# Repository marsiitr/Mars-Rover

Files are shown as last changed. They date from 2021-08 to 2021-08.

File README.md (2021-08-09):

# Mars-Rover

## Open Projects 2021   

## Abstract
<p align="justify">
 The <b>Mars Rover</b> is a small vehicle built to cover mars like uneven terrains. It is made to cover ueneven surfaces with ease and further to collect and analyze data. It has a robotic arm for data collection process and contains various sensors to recieve and record the data. It also has cameras, lidar and various other sensors for visual data interpretation and navigation.
</p>

<p align="center">
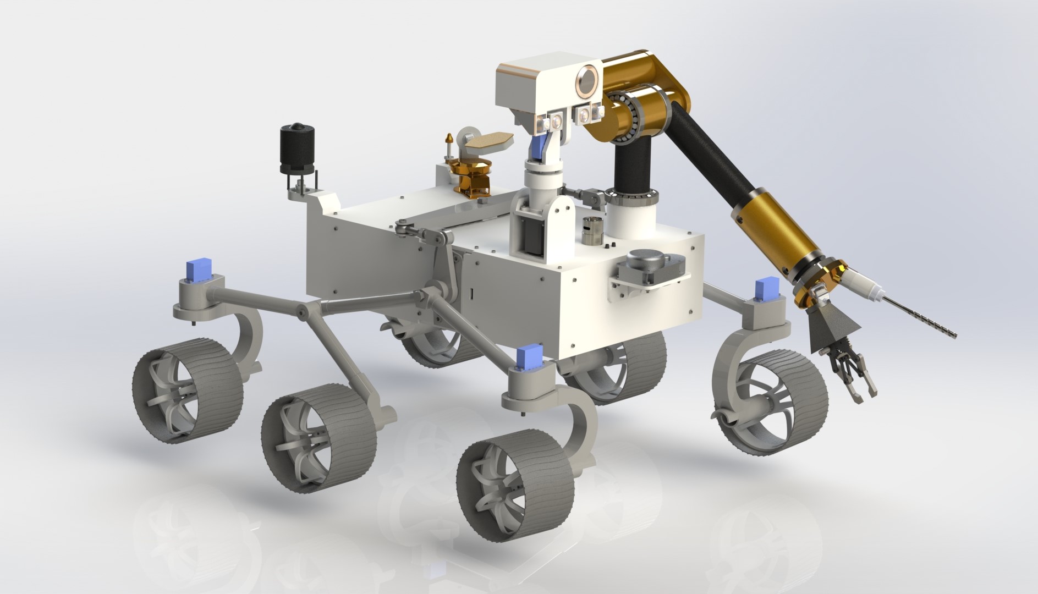
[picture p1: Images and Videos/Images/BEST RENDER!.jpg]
Mars Rover

 <i>Mars Rover</i>
</p>

## Motivation
The Mars rover project helps us to learn the mechanisms and functioning of an actual rover sent to Mars under various space programmes. 

<p align="justify">
 It gives us an insight on the <b>Rocker Bogie</b> suspension system which facilitates the best possible movement of the Rover on challenging terrains. It also compelled us to think about a mechainism for a compact and fully functioning robotic arm which would be used to collect sample data.
</p>

<p align="justify">
The project also sheds light on the various sensors used by the rover for data collection and analysis as well as for its navigation. <b>Lidar</b> and <b>PIXL</b> are the senosrs used by us in the rover. 
</p>

The project also helped us learn detailed CAD modelling using Solidworks.

## Mechanical aspects of design
 
### Chassis
<p align="justify">
The main body of the rover is built up using 20*20 sq.mm aluminium T slots as frames. It consists of a top and a bottom frame (each of 382 * 283 mm T slots) connected using a metal connector where the rocker bogie would be attached. Each rectangular frame is made up using 2 different pipes of length 382mm and 283 mm along with 2 extra 283mm pipes attached in between the frame to give it extra stability and support. It is then covered with ABS plastic covers which are attached to the frame using bolts and nuts.
</p>

<p align="center">  
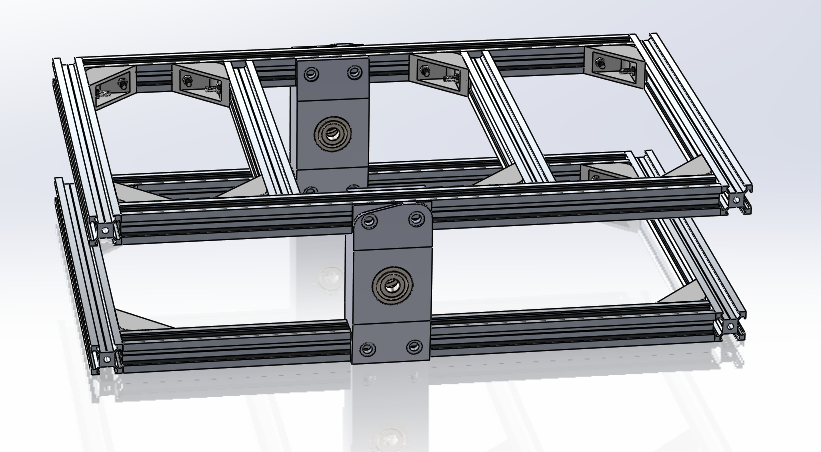
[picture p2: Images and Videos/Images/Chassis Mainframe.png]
Chassis
    
<i>Chassis</i>    
</p>  

### Rocker Bogie  
<p align="justify">
The Rocker Bogie is a six wheeled special suspension system used by the rover to ensure efficient motion on uneven terrains. It helps the mars rovers to overcome the rough terrains while maintaining stability by ensuring that all the wheel remain in contact with the ground. Each side of the suspension system is made up using 4 pipes of lengths 200, 170, 140 and 122mm(each of 314mm^2) which are connected using 3D printed connectors that facilitate the required motion of the suspension system. Both sides of the syspension are connected with the help of a differential bar placed on main frame of the rover. The middle of the bar is connected to the body with a pivot and the two ends are connected to the two rockers through some short links. If you hold the model rover body steady in midair and tilt one rocker up, one end of the bar will go back, the other end will go forward, and the other rocker will tilt down, thus maitaining the balance of the rover. 
</p>

<p align="center">
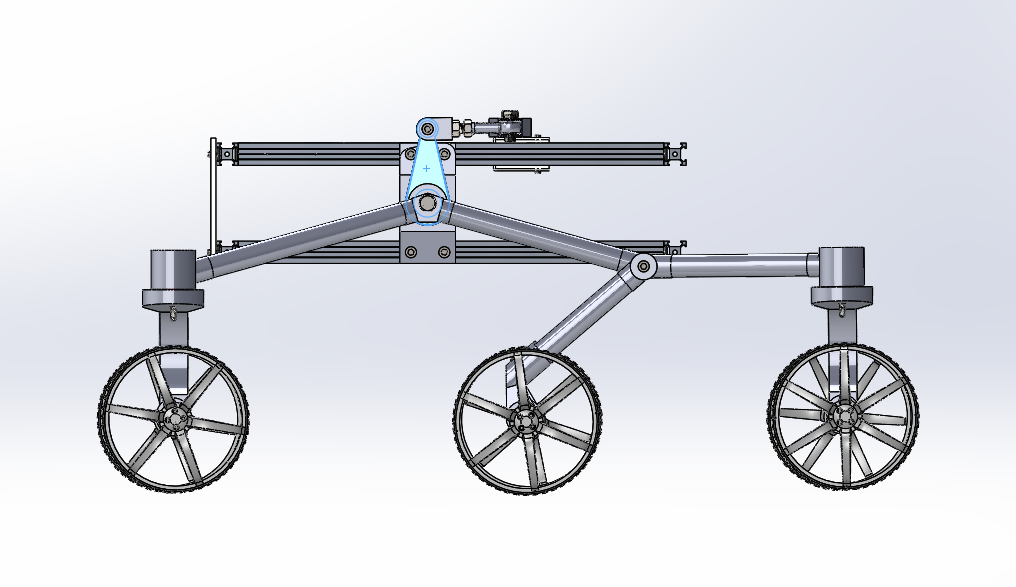
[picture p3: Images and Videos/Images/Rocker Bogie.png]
Rocker Bogie

 <i>Rocker Bogie</i>
</p>

### Robotic Arm
The robotic arm is equipped with three modules: a drill, a camera and a sample collector, installed on a rotating disc.

It has 4 degrees of freedom(DOFs) as follows:  
1.The base can be rotated 360 degrees.  
2.The rotational joint can be rotated 180 degrees (range is limited by the counterweight)  
3.The main link contains a hydraulic/pneumatic cylinder which is used to extend/shorten the length of the link. The length of the link has a range of 33-43 cm.   
4.The rotating disc is used to engage either the drill or the sample collector with the Martian surface at a time.  

Thus, in a way, we have a handle on the three polar coordinates:
1. The base varies the planar angle 'theta'
2. The rotational joint varies the vertical angle 'phi'
3. Hydraulic/pneumatic cylinder varies radial distance 'r'
This makes inverse kinematics relatively simpler.
 
<p align="justify">
The camera is used all the time for navigation of the arm as well as scanning of the martian surface
Servo motors are used for precise actuation.
An air compressor/pump embedded in the rover body is used to create the necessary pressure differential to operate the pneumatic/hydraulic cylinder.
</p>

<p align="center">
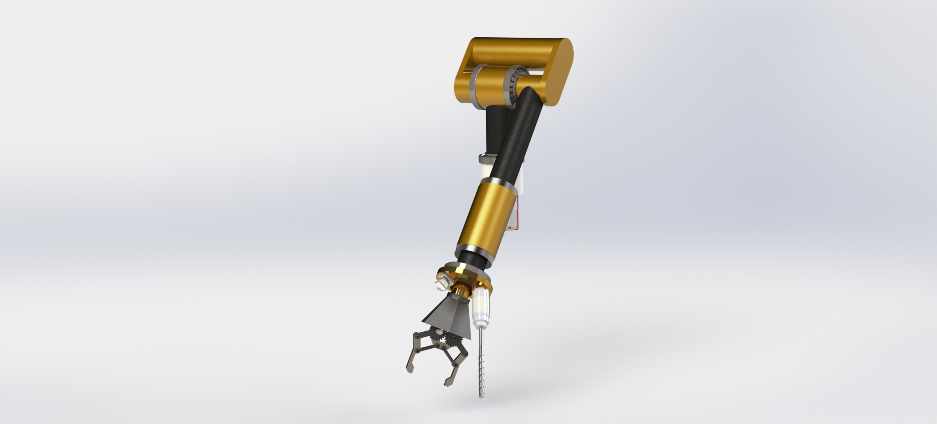
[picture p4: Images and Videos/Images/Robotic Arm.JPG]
Robotic Arm
  
<i>Robotic Arm</i>
</p>
                                                                                                                                                 
### Wheels
The wheel can be 3D by more flexible materials like thermoplastic elastomers which has high impact strength and

### Mast Cam
<p align="justify">
The bottom part of the mast contains the stepper motor which is fixed to the body. A shaft extends to the upper part of the mast which can rotate horizontally and lies on a cylindrical thrust bearing. The camera is attached to the mast with the servo motor for vertical rotation.
</p>

<p align="center">
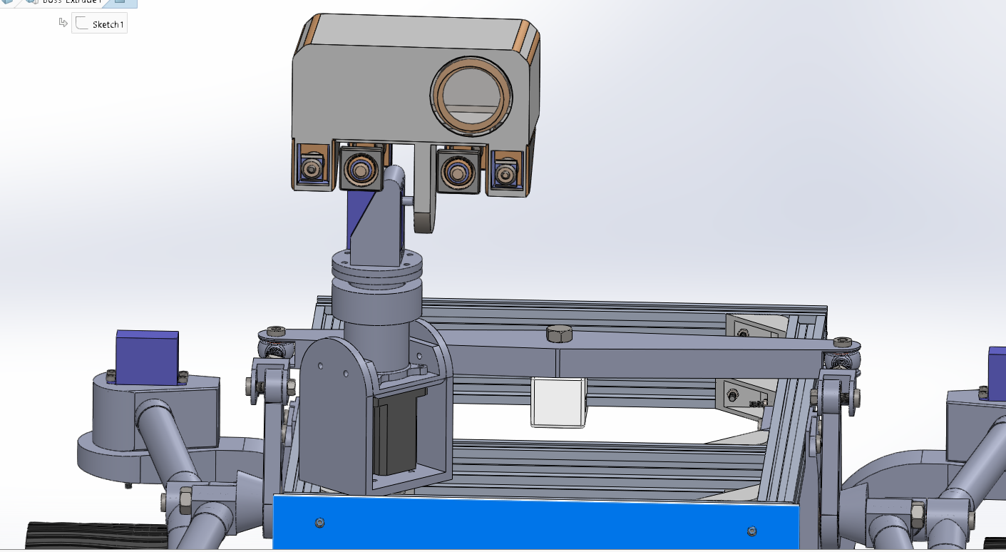
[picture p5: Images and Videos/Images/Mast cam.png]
Mast Cam
Mast Cam</i>
</p>

## CAD PARTS:
**IN CASE OF DISCREPANCY IN DOWNLOADING THE PARTS, KINDLY CHECK THE GIVEN DRIVE LINK:** https://drive.google.com/drive/folders/1dSjtfLlo9qPeHwJP8TGqEmEa5Fyg8wRc?usp=sharing

## Electronics aspects of design

### Sensors
1. **LIDAR sensor:**
<p align="justify">
Lidar is an acronym for “light detection and ranging.” It is sometimes called “laser scanning” or “3D scanning.” The technology uses eye-safe laser beams to create a 3D representation of the surveyed environment. This helps in navigation as well as analyzing the surrounding terrains and thus aids in the research part of the rover mission.
</p>

<p align="center">
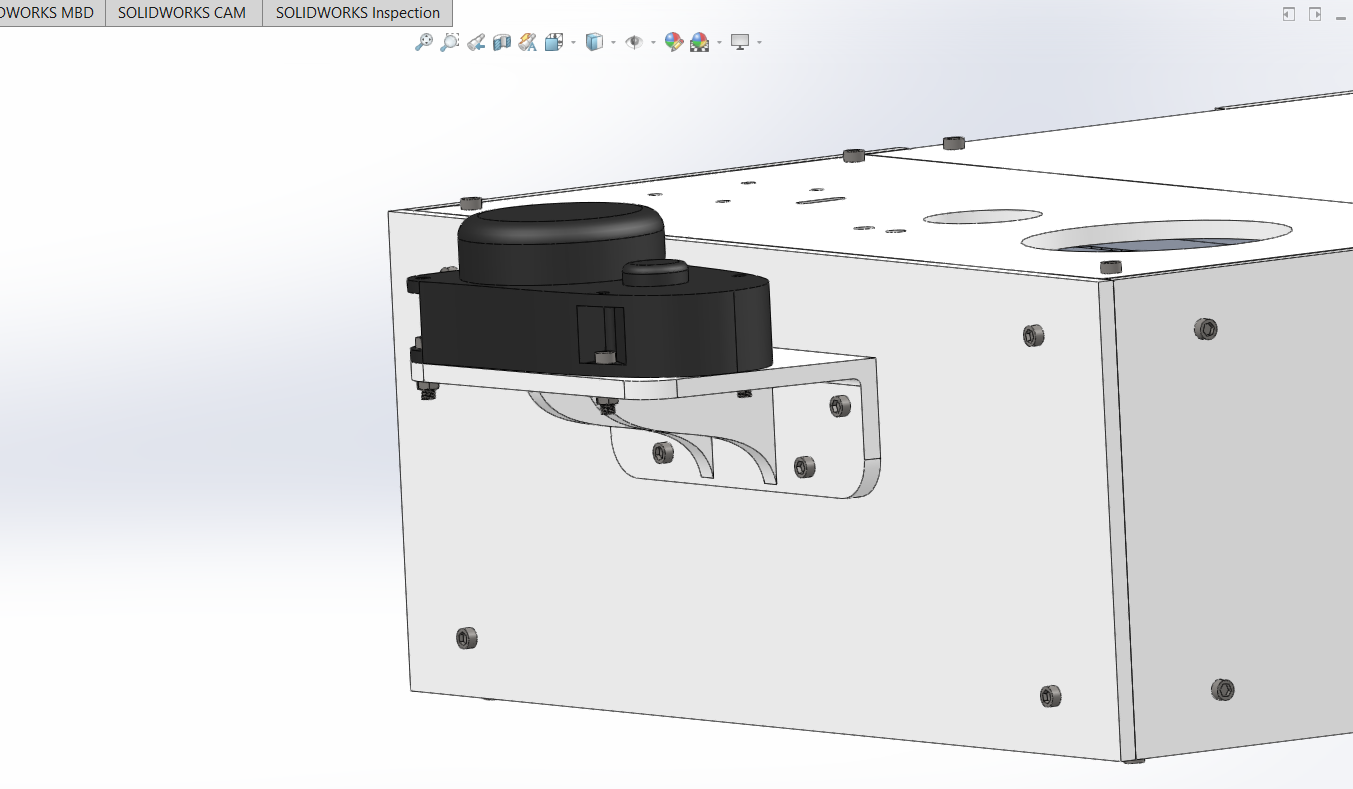
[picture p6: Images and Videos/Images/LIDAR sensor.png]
LIDAR Sensor

 <i> LIDAR Sensor</i>
</p>

2. **Mast Cam:**
<p align="justify">
The Mast Cam mounted over the chassis is used to get high definition videos and 3D-images of the surroundings which can be used for research purposes. It also has high zoom focus which can help in detailed examination of distant objects.
 </p>

3. **Robotic arm camera:**
<p align="justify">
A small camera is mounted on of the three modules of the robotic arm to assist in its motion and guide the drill to the required position. This makes teh collection of data sample more precise and accurate.
</p>

### Actuators
1. **DC motors:**
<p align="justify">
Six 12V DC motors with 20 RPM output are to be attached to the wheels which causes the locomotion of the Rover. The are placed in a holder attached to the Rocker Bogie and transmit torque to the wheels with the help of a small 3D printed shaft joining both these parts.
</p>

2. **Servo Motor:**
<p align="justify">
Four digital servo motors with 25kg cm torque output and operating voltage of 4.8-6.8 volts are used for steering the rover. The are attached to the rocker bogie with the help of a 3D printed holder connected on top of the dc motor holder. It enables the turning of front and rear pair of wheels and thus helps in turning the rover.
</p>

3. **Stepper motor:**
<p align="justify">
A 45kg-cm torque stepper motor is used for the horizontal rotation of the mast cam. The shaft of the stepper motor is attached to a threaded rod with a shaft coupler which transfers the rotation to the top part of the mast.
</p>

## Research part
<p align="justify">
We did an extensive research on the previously sent Mars Rovers and extracted details about the different components of the rover. We looked upon the structure and functioning of the parts and decided accordingly what to put in our rover. Although it was not practical to use all senosors and parts used by high end mars missions, we added whatever was possible in our reach to aid the research work of the rover.  
</p>

**This is the link of our initial research doc:** https://docs.google.com/document/d/1-jrgd7fFMnukzN-lmV8PeAjKU0p7QLTJImEPwY9DrF8/edit

## Cost Structure

| Components | Cost (in INR) |
|:---:|:---:|
| ABS plastic for 3d printing  | 16000 |
| T-slot Aluminium Extrussion | 360 |
| Battery  | 4300|
| Camera| 1500 |
| Stepper motors  | 725 |
| DC motors  | 3800 |
| Servo motors| 11250 |
| Servo horns | 375 |
| End joints | 800 |
| Nut and Bolts | 700 |
| Bearings | 900 |
| Lidar | 4850  |
| 4 thrust roller bearings| 3800 |
| Double acting mini pneumatic cylinder | 1258 |
| Single piston air compressor | 1000|
| Pneumatic tubing| 950 |
| Drill | 850 |
| Dc motor for drill: 15volt 11 watt | 3900 |
| Base servo motor 12volt  | 4950  |
| Joint servo motor 12volt |4950|
| Disc servo motor 12volt 2.9 watt| 3950 |
| Camera | 1250 |
| Sampler mechanism 5volt servo motor | 250 |
| Miscellaneous | 1500 |
|Total Cost| 74168 |

## Applications
1. The rover can be used to research the areas with highly uneven terrains and surfaces with ease due to its Rocker bogie suspension system.
2. It is equipped with a robotic arm and drill which enables sample data collection and storage.
3. The rover consists of a camera to take 3D images and high definition videos for mapping the terrain as well as analyzing it scientifically.
4. It can also be used to analyze the collected samples using the various sensors present on the rover

## Limitations
1. Speed of the rover is very low even on the flat terrains.
2. Battery life of the rover is short due to less charging capacity.

## Future Improvement
1. Better materials could be used instead of 3D printed plastic.  
2. Simulating the model in Gazebo and ROS.  

## Team members (with GitHub IDs)
1. <a href="https://github.com/matbot1">Avinash Singh</a>
2. <a href="https://github.com/MurkeyCube">Harikrishnan PB</a>
3. <a href="https://github.com/Pratyush-932">Pratyush Ojha</a>
4. <a href="https://github.com/SambitPrabhu">Sambit Prabhu</a>

## Mentors:
1.<a href="https://github.com/vanshgoyal">Vansh Goyal</a>

## Reference links
**Youtube-**  
<a href="https://www.youtube.com/watch?v=NOZZMsMAGh0&t=142s"> How I build mars rover replica </a>   
<a href="https://www.youtube.com/watch?v=McydwwR8xu4">[Mars Rover 2020 Perseverance] Body Assembly</a>  
<a href="https://www.youtube.com/watch?v=007SnaUxi40">JPL Mars Science Laboratory The Curiosity Rover</a>   

**Research links-**  
<a href="https://www.hindawi.com/journals/ijae/2016/5181097/"> Rocker Bogie Research </a>   
<a href="https://mars.nasa.gov/mars2020/spacecraft/rover/"> NASA Mars Rover (Perseverance) </a>   
<a href="https://llis.nasa.gov/lesson/11501">Actuator Design process for curiosity</a>     
<a href="http://robotics.estec.esa.int/ASTRA/Astra2004/Papers/astra2004_D-05.pdf">Types of Rocker Bogies</a>  
<a href="https://teamares.sserd.org/project_files/Ares_MCEV_Report.pdf"> Research paper for design of crew exploration vehicle on Mars</a>

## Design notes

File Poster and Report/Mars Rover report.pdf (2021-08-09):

# Mars Rover

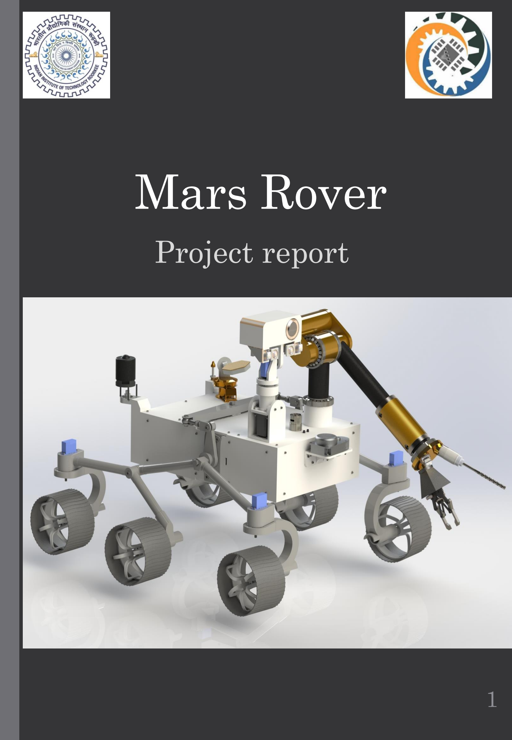
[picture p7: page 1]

## Project report

# INDEX

Team Members | -3
Abstract | -4
Motivation | -4
Research | -5
Mechanical Aspects | -6
Electronic Aspects | -13
Applications | -15
Limitations | -16

### Further Improvements -16

Reference Links | -17

# Mentor

### Avinash Singh

### Harikrishnan P B

### Pratyush Ojha

### Sambit Prabhu

# Team Members

### Vansh Goyal

# ABSTRACT

We have designed a mars rover capable of moving on rough terrains, with stable body frame and a fully functioning robotic arm, capable of drilling and collecting samples from the surface. The rover can move forward, backward and rotate. The navigation is done with the help of the mastcam which can orient itself in the desired direction.

# MOTIVATION

Having seen the successful landing of Mars missions, we were curious to find out how the rover is able to navigate in such harsh conditions and are able to carry out scientific missions on other planets.

# RESEARCH

1) In-depth study of NASA’s Perseverance and Curiosity Rover.
2) Components, instruments and features systematically documented.
3) Researched various types of suspension systems and we found the rocker bogie best as it requires less maintenance, and all the wheels stay in contact with the ground.
4) We chose the sensors required for the navigation of the rover.
5) The robotic arm was designed to be able to drill and collect the samples.
6) Most of the parts are designed to be 3D printed and can be assembled or disassemble easily.

# MECHANICAL ASPECTS

## 1) Chassis:

- The main frame of the rover is made by 20mm x 20mm T-slot Aluminium extrusion. The aluminium extrusions are connected with the help of 3D printed connectors.

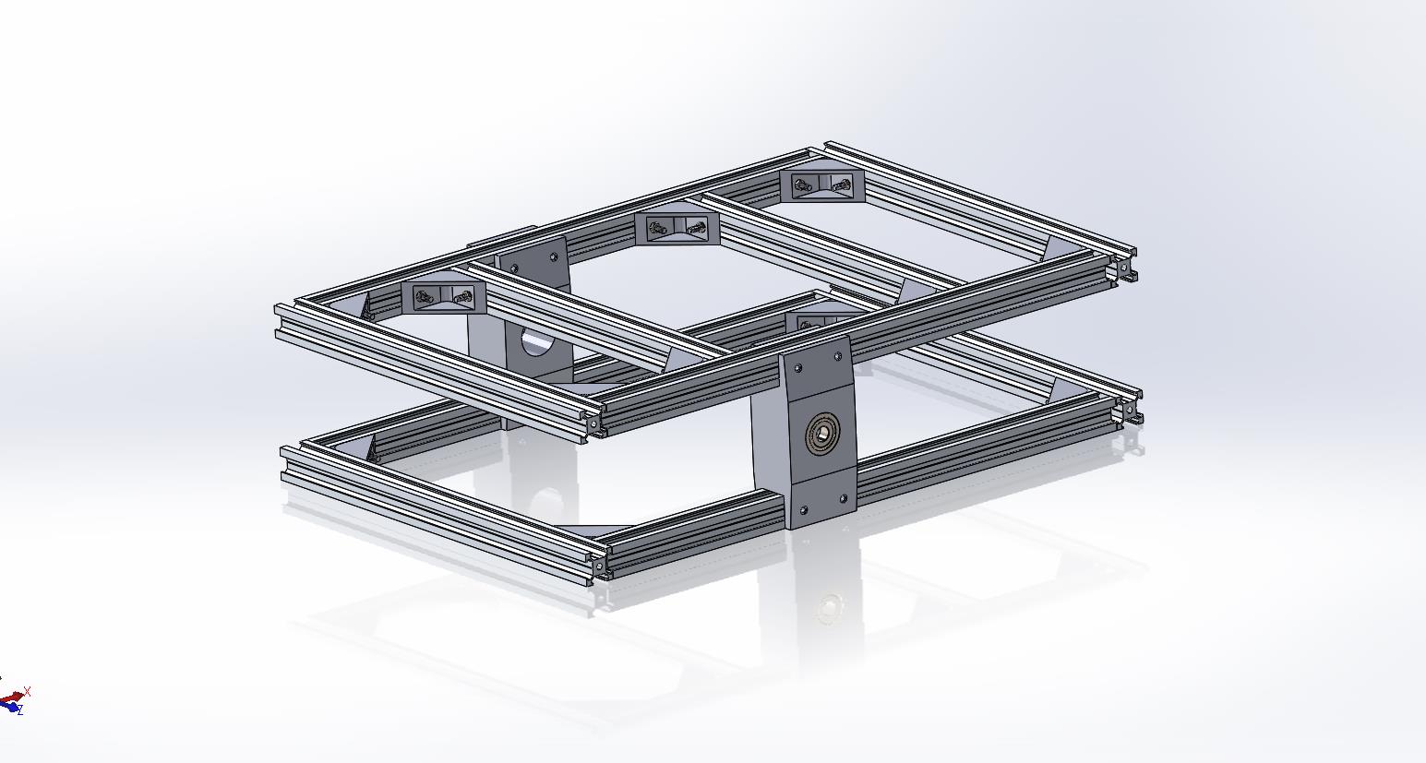
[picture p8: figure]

## 2) Rocker bogie:

- The rocker bogie
system maintains a
relatively constant
weight on each of
the rover's wheels.
The suspension also
minimizes rover tilt
as it drives, keeping
it more stable.

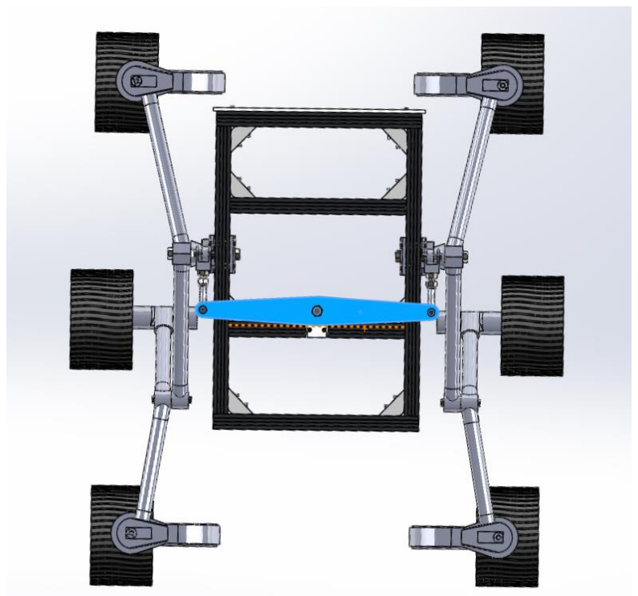
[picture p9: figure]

- The rocker bogie is made with a differential connected to the body of the rover for stability.
- The differential connects the left and right rockers and connects to the body of the rover by a pivot point in the centre of the rover’s top deck.

- We decided on 6 wheeled rocker bogie, so we have three main parts for the rocker bogie-
- The first one is the rocker which connects the front wheel to the differential and bogie in the rear.
- The second one is the bogie which connects the middle and rear wheel to the rocker.
- The third one is the connector for the front and back wheel to the rocker bogie for steering and rotation.

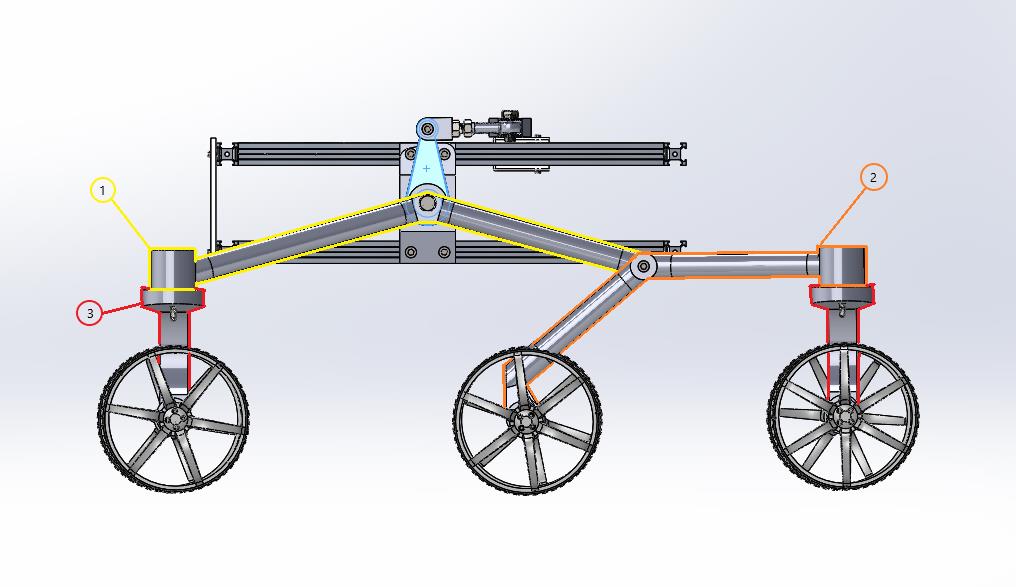
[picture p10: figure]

## 3) Wheel:

- The wheel can be 3D printed by more flexible materials like thermoplastic elastomers which has high impact strength and wear resistant.

## 4) Mastcam:

- the bottom part of the mast contains the stepper motor which is fixed to the body. A shaft extends to the upper part of the mast which can rotate horizontally and lies on a cylindrical thrust bearing. The camera is attached to the mast with the servo motor for vertical rotation.

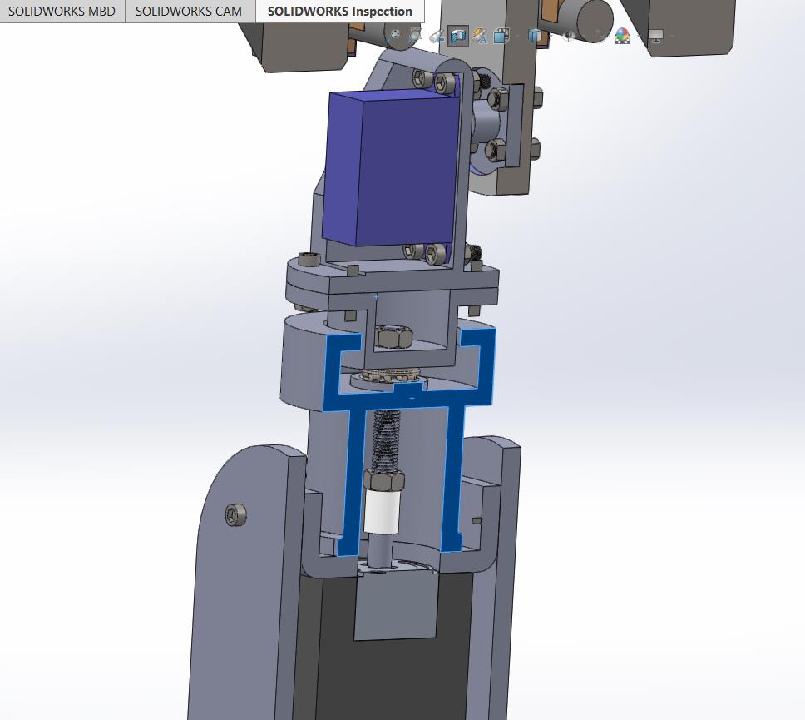
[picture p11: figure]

## 5) Robotic Arm:

- The robotic arm is
equipped with three
modules: a drill, a
camera and a
sample collector,
installed on a
rotating disc.

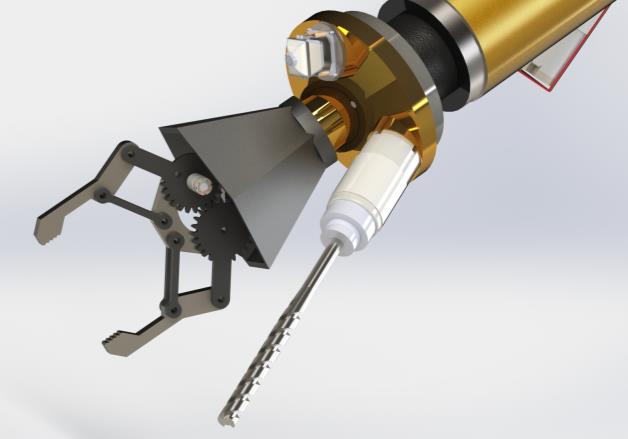
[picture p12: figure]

- It has 4 degrees of freedom(DOFs) as follows:
1) The base can be rotated 360 degrees.
2) The rotational joint can be rotated 180 degrees (range is limited by the counterweight)
3) The main link contains a hydraulic/pneumatic cylinder which is used to extend/shorten the length of the link. The length of the link has a range of 33-43 cm.

4)The rotating disc is used to engage either the drill or the sample collector with the Martian surface at a time.

Thus, in a way, we have a handle on the three polar coordinates:

1. The base varies the planar angle 'theta'
2. The rotational joint varies the vertical angle 'phi'
3. Hydraulic/pneumatic cylinder varies radial distance 'r'

This makes inverse kinematics relatively simpler.

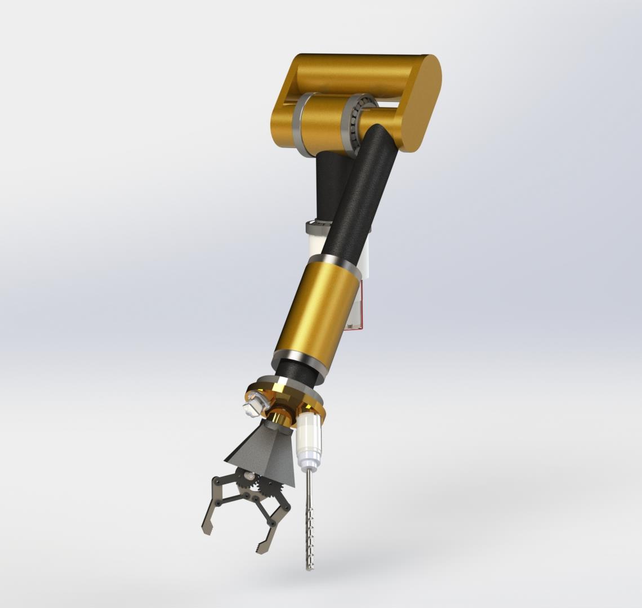
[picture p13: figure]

- The camera is used all the time for navigation of the arm as well as scanning of the Martian surface.
- Although the links of the robotic arm are light, the weights of the various motors and other
components in the end effector cause dynamic instability, which necessitates the usage of a counterweight.
- The counterweight provides frontback stability to the arm, as well as distributes the load between the two left-right bearings that are mounted on the base, so as to minimize the chances of
mechanical failure.
- Servo motors are used for precise actuation.
- An air compressor/pump embedded in the rover body is used to create the necessary pressure differential to operate the pneumatic/hydraulic cylinder.

# ELECTRONIC ASPECTS

## 1) Actuators:

a) 12V Brushless DC motors are attached to the wheels and used for the locomotion of the rover.
b) Servo motor is used for the movement of the corner four wheels, the head of the mastcam and in the robotic arm.
c) Stepper motor for the horizontal rotation of the camera. The shaft of the stepper motor is attached to a threaded rod with a shaft coupler which transfers the rotation to the top part of the mast.

## 2) SENSORS:

a) Mastcam:

It is used to take images and navigate the rover and can change its orientation to a desired location.

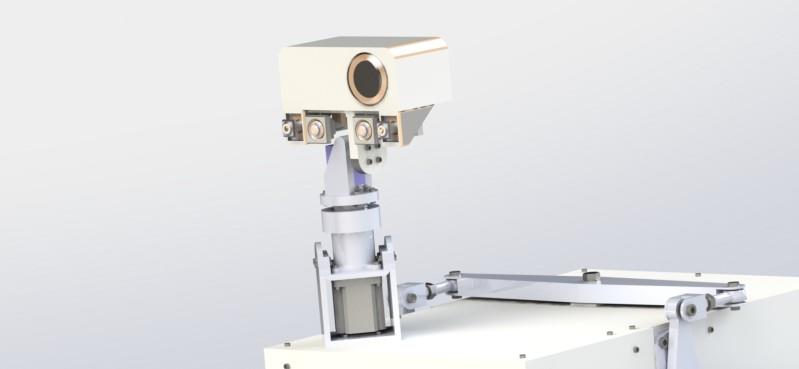
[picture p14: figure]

b) Lidar:

It is used for sensing the distance between the rover and its
surrounding and helps in
navigation.

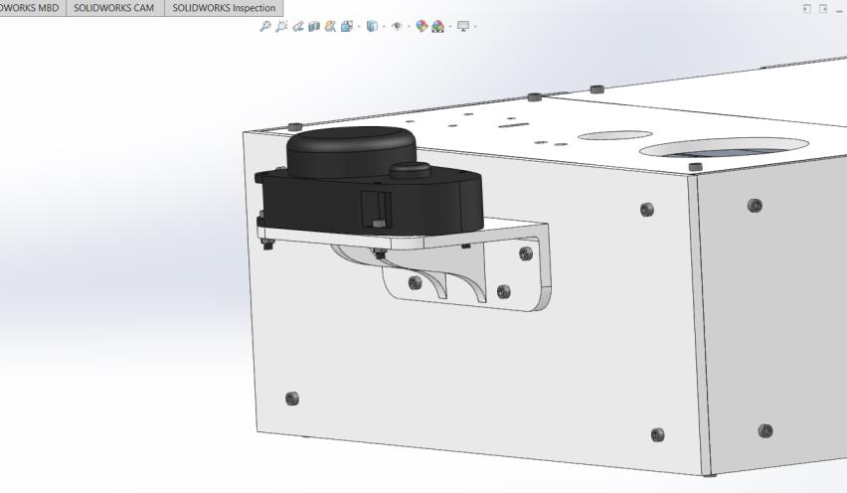
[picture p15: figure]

# APPLICATIONS

- The rover can be used to research the areas with highly uneven terrains and surfaces with ease due to its rocker bogie suspension system.
- It is equipped with a robotic arm and drill which enables sample data collection and storage. The rover consists of a camera to take 3D images and high-definition videos for mapping the terrain as well as analyzing it scientifically.
- It can also be used to analyze the collected samples using the various sensors present on the rover

# FUTURE IMPROVEMENTS

1) Better materials could be used instead of 3D printed plastic.
2) Simulating the model in Gazebo and ROS.

# LIMITATIONS

1) The speed of the rover is slow.
2) Life of the rover is short since the charging capacity is less.

# REFERENCE LINKS

Youtube-
- [Mars Rover 2020 Perseverance] Body Assemblyhttps://www.youtube.com/watch?v=McydwwR8xu4
- How I build mars rover replicahttps://www.youtube.com/watch?v=NOZZMsMAGh0&t=1 42s (https://www.youtube.com/watch?v=NOZZMsMAGh0&t=142s)
- JPL Mars Science Laboratory The Curiosity Roverhttps://www.youtube.com/watch?v=007SnaUxi40

Research links-
- https://www.hindawi.com/journals/ijae/2016/5181097/
- https://mars.nasa.gov/mars2020/spacecraft/rover/
- https://llis.nasa.gov/lesson/11501
- http://robotics.estec.esa.int/ASTRA/Astra2004/Papers/astra2004_D-05.pdf (http://robotics.estec.esa.int/ASTRA/Astra2004/Papers/astra2004_D-05.pdf)
- https://teamares.sserd.org/project_files/Ares_MCEV_Repo rt.pdf (https://teamares.sserd.org/project_files/Ares_MCEV_Report.pdf)

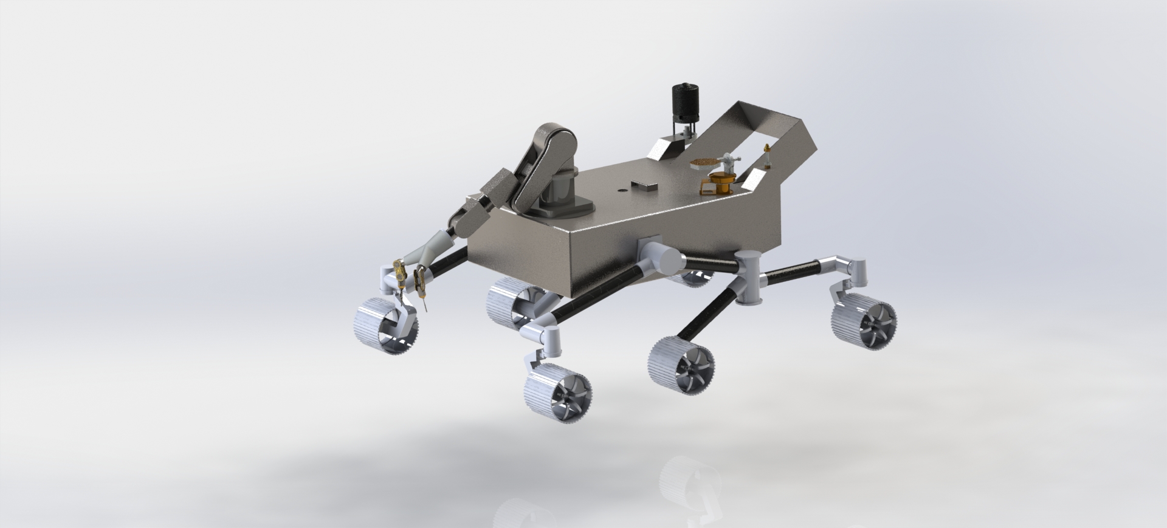
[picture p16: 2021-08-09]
Images and Videos/Images/Initial design (changed later).JPG

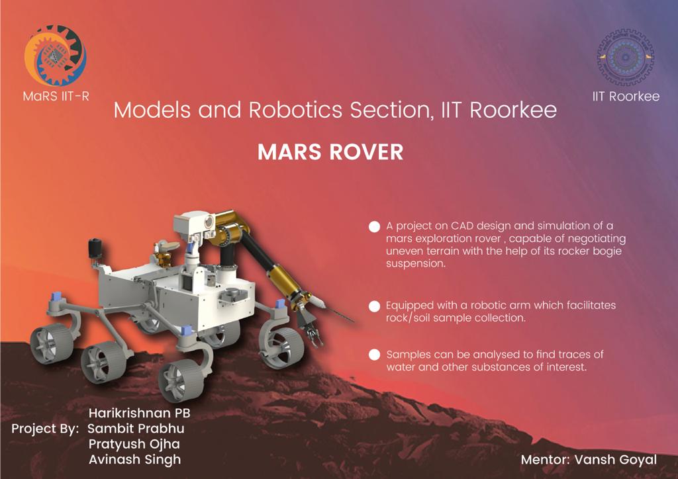
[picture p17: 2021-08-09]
Poster and Report/Poster.jpeg

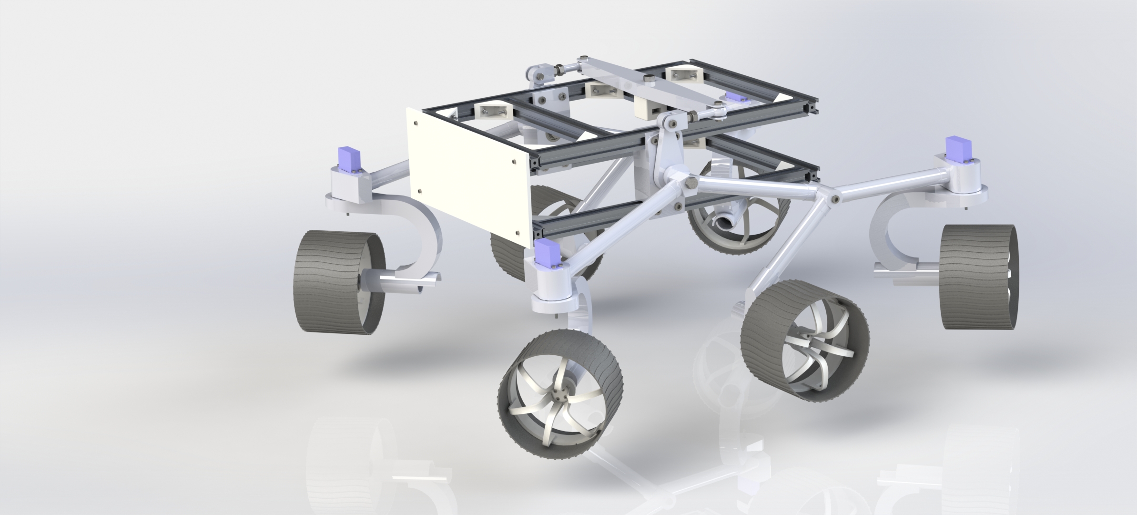
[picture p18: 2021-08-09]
Images and Videos/Images/Mars Rover 2.JPG

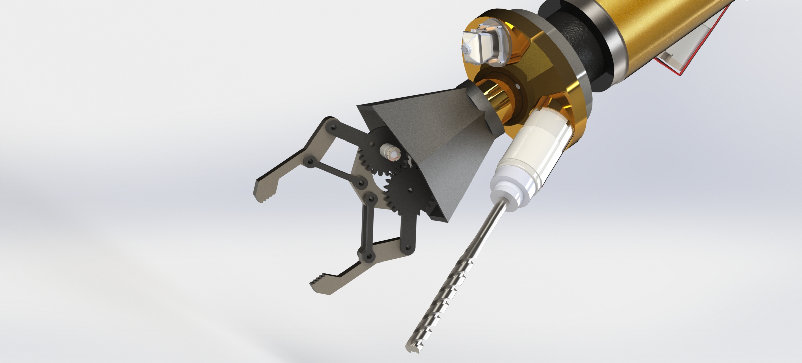
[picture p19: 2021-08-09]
Images and Videos/Images/Arm module.JPG

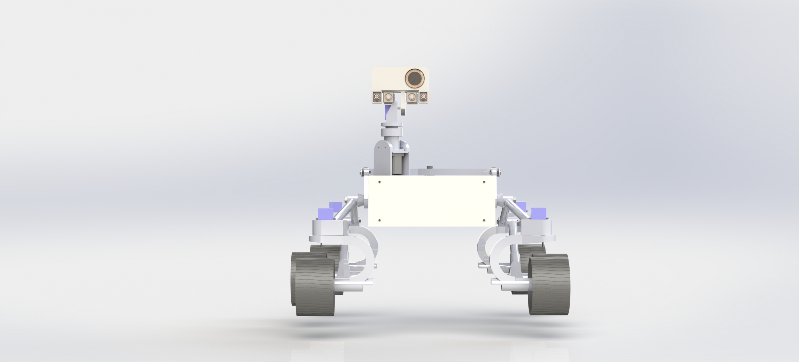
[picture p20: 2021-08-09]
Images and Videos/Images/camera 1.JPG

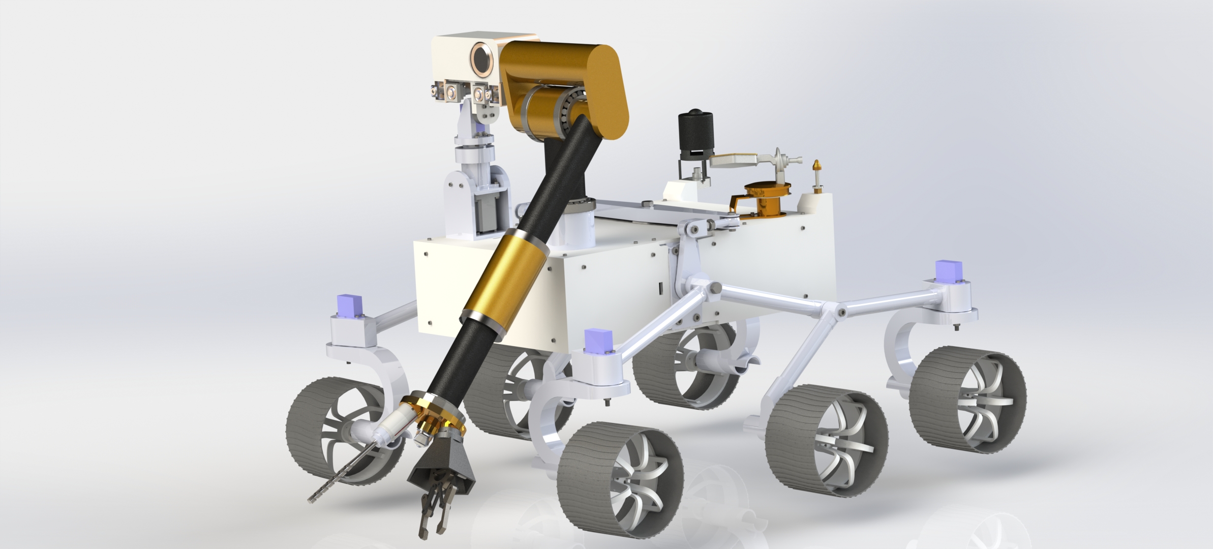
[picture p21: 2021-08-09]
Images and Videos/Images/rendered image 1.JPG

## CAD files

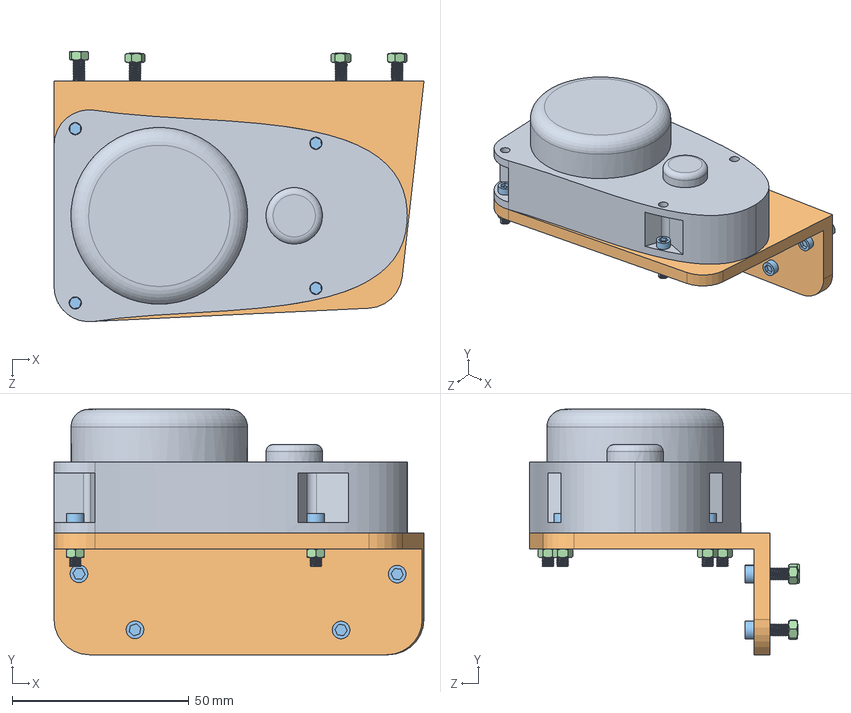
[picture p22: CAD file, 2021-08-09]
Mechanical design/Camera/Lidar/Lidar sensor.SLDASM
104.7 x 69.5 x 76.6 mm
Lidar
Stand for lidar
M3 bolt for camera-1 x 8
M3 nut x 8

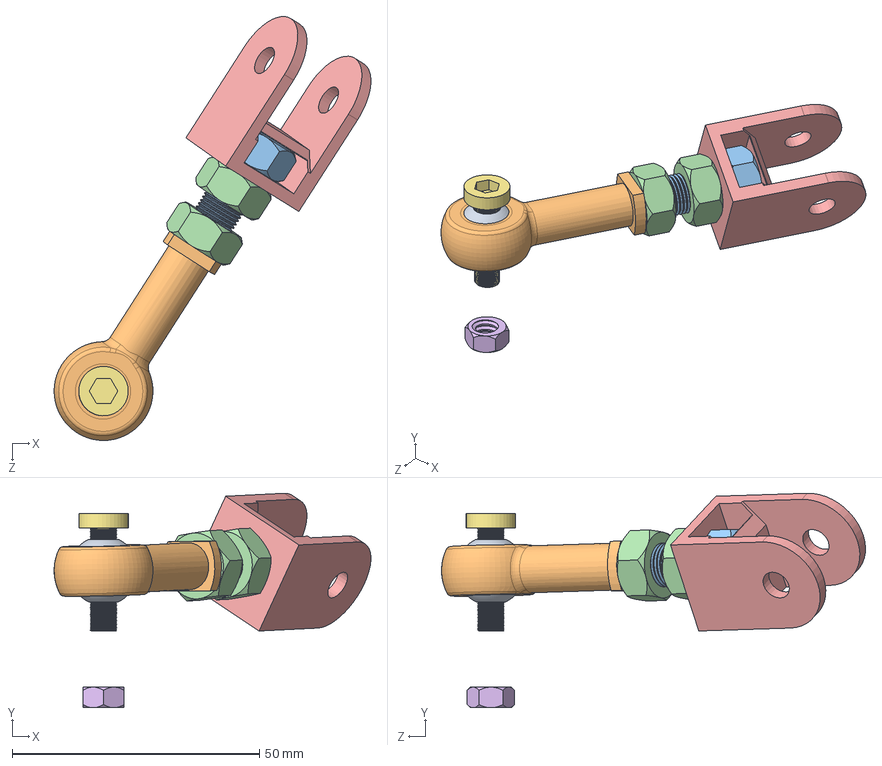
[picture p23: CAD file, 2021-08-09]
Mechanical design/Rocker Bogie/End joint bearing/End join bearing.SLDASM
64.1 x 43.3 x 85.7 mm
Ball
connector part
M8 Bolt for end joint
M8 Nut x 2
connector to rocker
M5 nut
M5 bolt for end joint

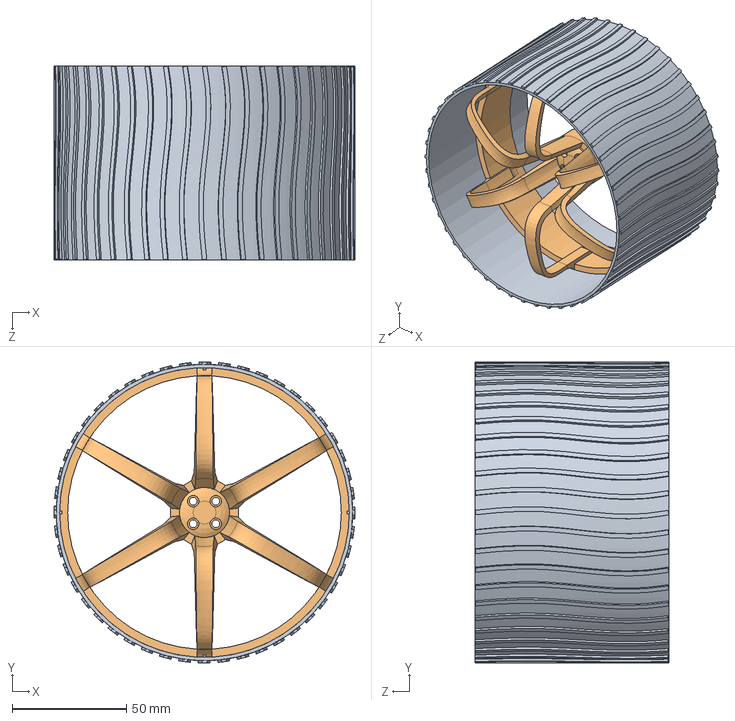
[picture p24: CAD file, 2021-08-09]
Mechanical design/Wheel.SLDASM
132.0 x 132.0 x 85.0 mm
Wheel Part-1
Wheel Part-2

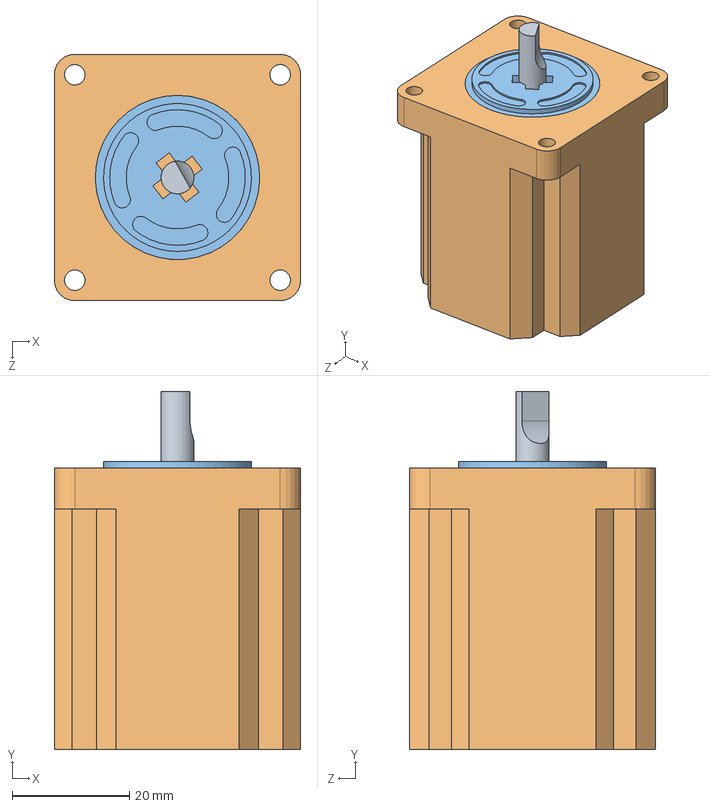
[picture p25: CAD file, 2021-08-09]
Mechanical design/Camera/Stepper motor/Stepper motor.SLDASM
42.0 x 61.0 x 42.0 mm
shaft for stpmotor
stepper motor-1
stepper motor-2

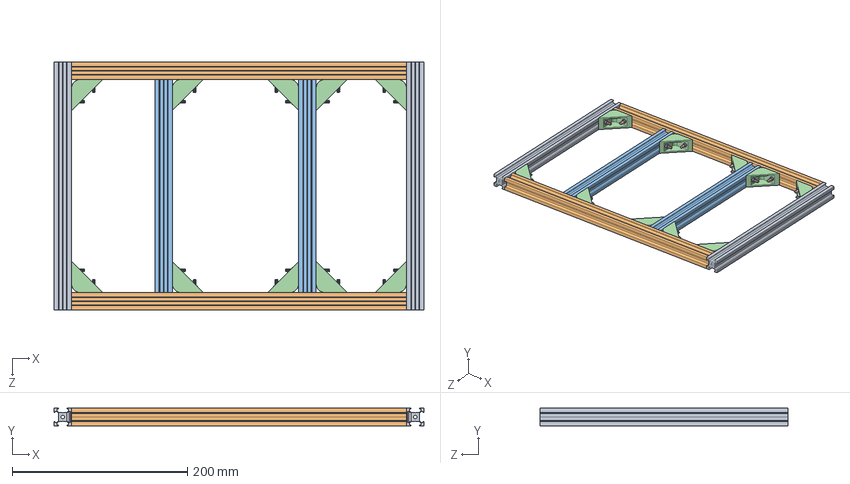
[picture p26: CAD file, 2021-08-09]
Mechanical design/Frame/Top Frame.SLDASM
422.0 x 20.0 x 283.0 mm
T-slot aluminium profiles(283) x 2
T-slot aluminium profiles(382) x 2
T-slot aluminium profiles(243) x 2
connector x 10
T-bolt x 20
hexagon nut style 1_is x 20

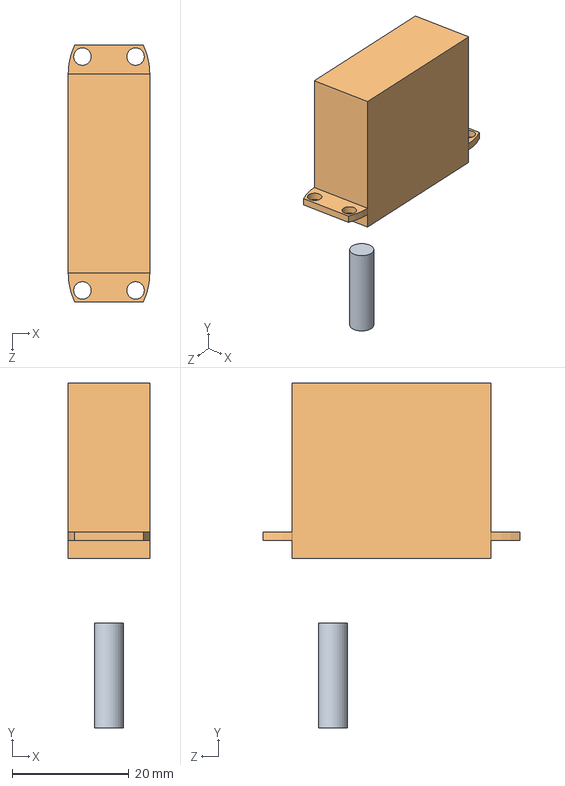
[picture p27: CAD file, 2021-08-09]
Mechanical design/Rocker Bogie/Motors/Servo Assembly.SLDASM
14.0 x 59.1 x 44.0 mm
servo shaft
Servo motor

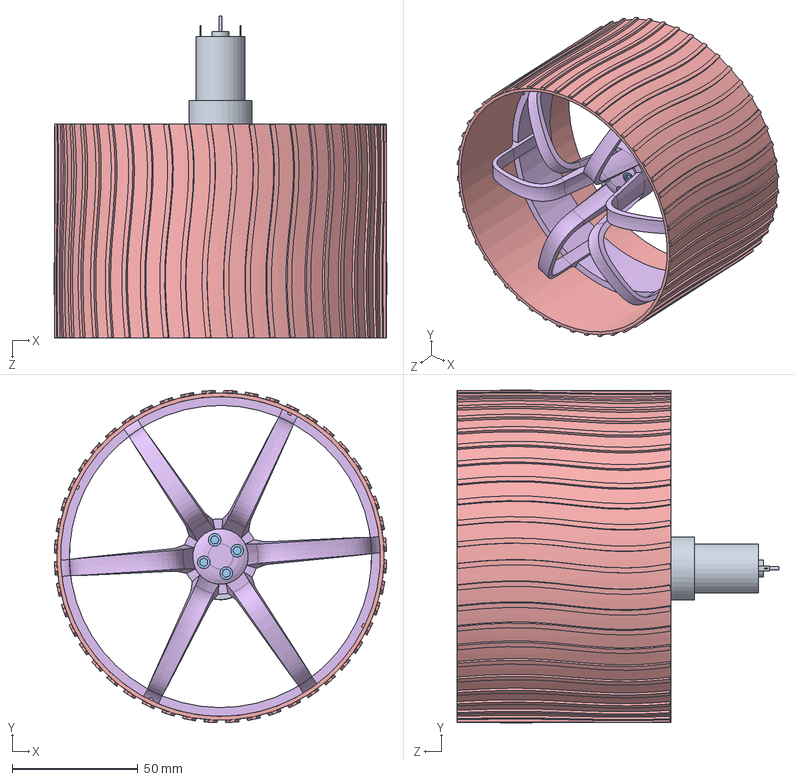
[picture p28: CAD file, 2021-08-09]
Mechanical design/Wheel + motor for centre.SLDASM
132.1 x 132.1 x 127.9 mm
Wheel motor(RH)
connector to wheel(RH)
M3 bolt for wheels(RH) x 4
M3 nut x 4
Wheel Part-1
Wheel Part-2

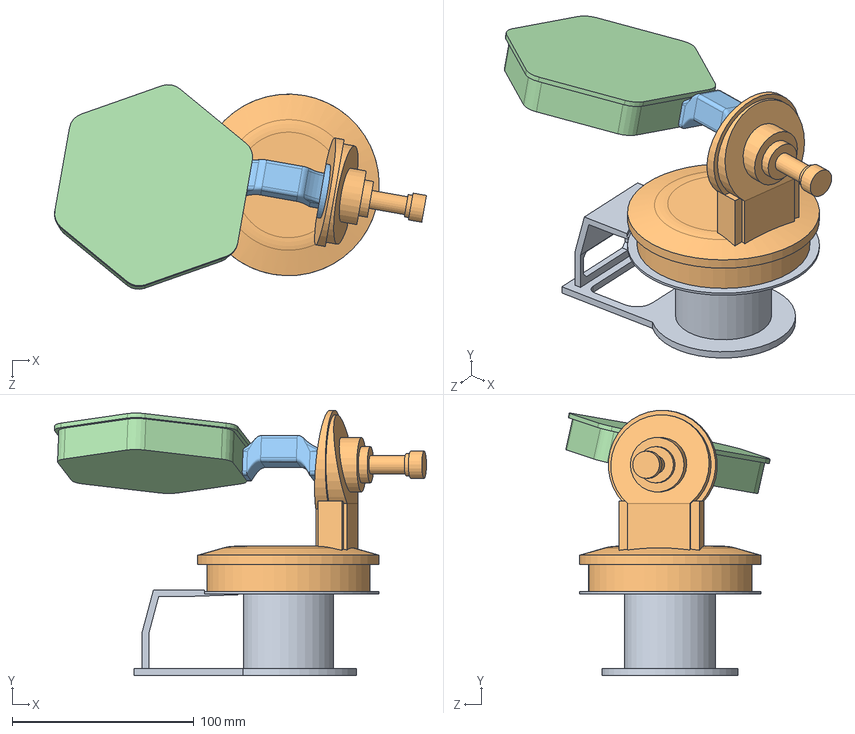
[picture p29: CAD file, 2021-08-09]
Mechanical design/Antenna/High Gain Antenna.SLDASM
204.9 x 146.0 x 112.6 mm
High Gain Antenna (Part 1)
High Gain Antenna (Part 2)
High Gain Antenna (Part 3)
High Gain Antenna (Part 4)

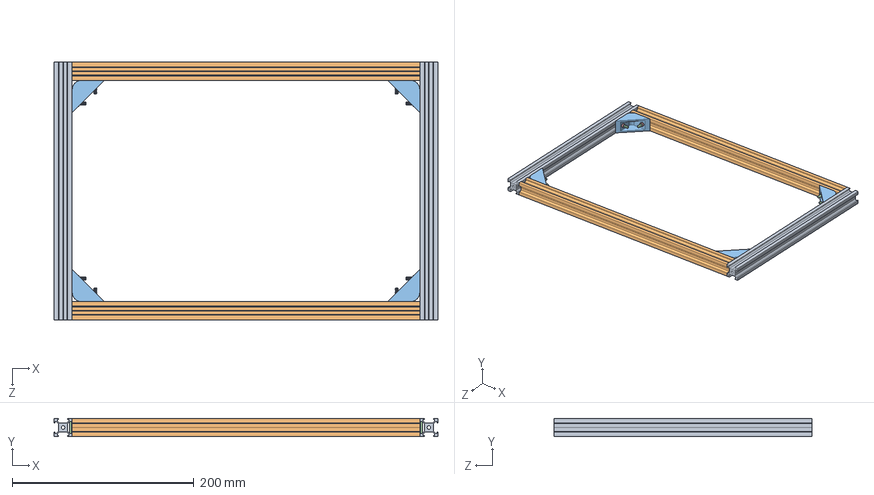
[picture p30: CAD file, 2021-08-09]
Mechanical design/Frame/Bottom Frame.SLDASM
422.0 x 20.0 x 283.0 mm
T-slot aluminium profiles(283) x 2
T-slot aluminium profiles(382) x 2
connector x 4
T-bolt x 8
hexagon nut style 1_is x 8

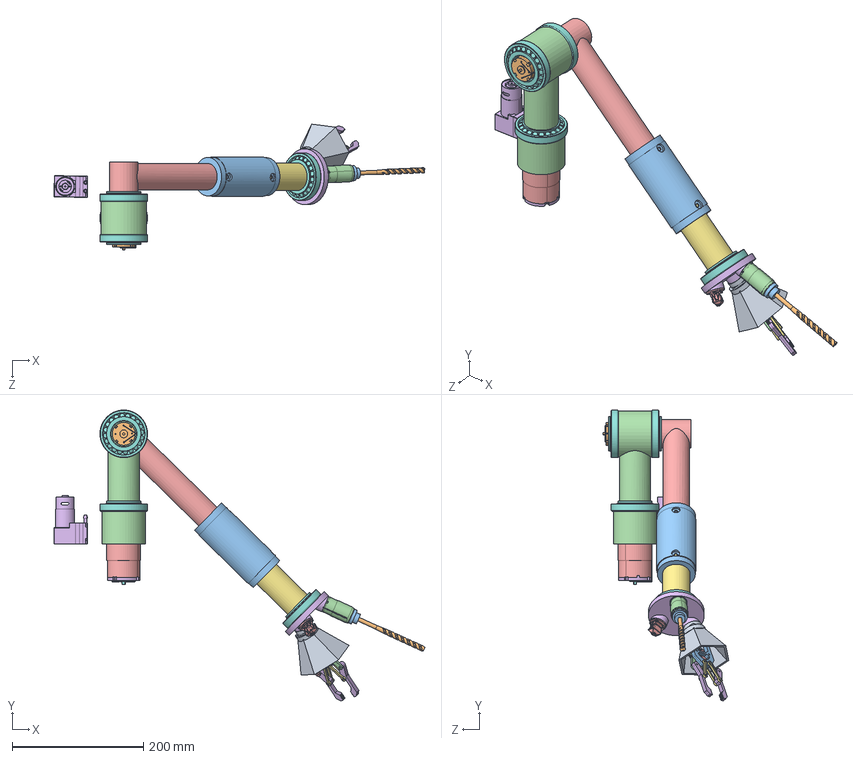
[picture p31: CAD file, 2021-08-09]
Mechanical design/Robotic arm/OPEN THIS ASSEMBLY just robotic arm.SLDASM
564.7 x 442.8 x 191.4 mm
Arm 01
Arm 02 x 2
Arm 03 x 2
Arm 04
Arm 05
Arm 07 x 4
Arm 06 x 4
Smol motor 2
cover for gripper
DRILL
Drill connect
Medium motor
camera
Three module
arm to module tube
Tapered roller bearing x 4
Large motor custom shaft
Large motor scaled part x 2
pneumatic cylinder
Base cylinder
body Geometry.stp
Bott.stp
ARMICHER19V.stp
shaft.stp
Baring.stp
Wire.stp
Large motor custom shaft coupler x 2
base to joint tube
joint to hydraulic tube
Mini Air Pump Compressor 12 V TYAP127

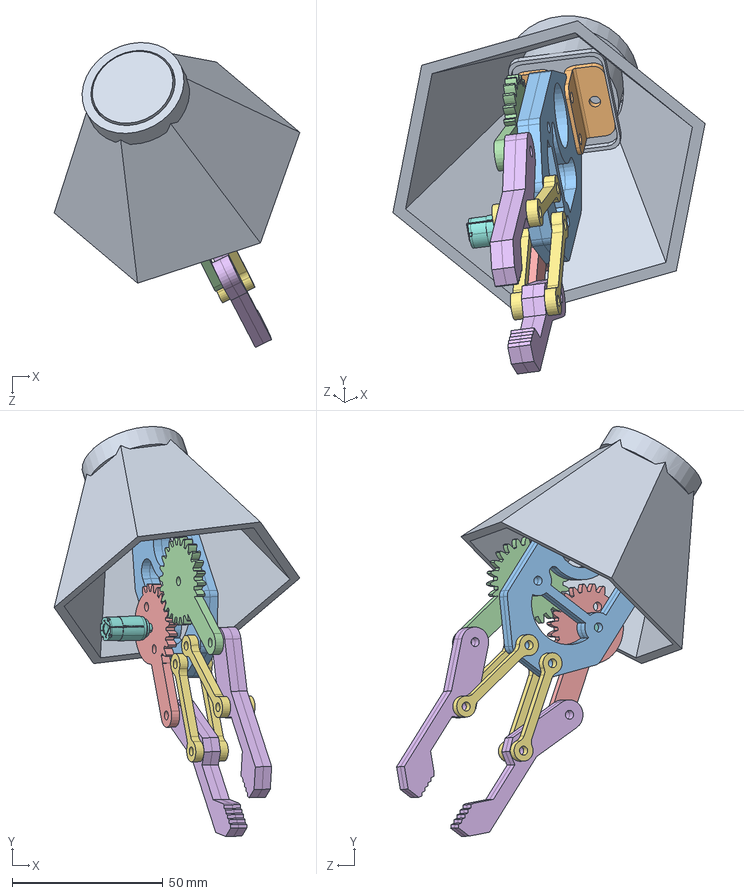
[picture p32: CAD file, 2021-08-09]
Mechanical design/Robotic arm/sample.SLDASM
81.5 x 136.1 x 101.2 mm
Arm 01
Arm 02 x 2
Arm 03 x 2
Arm 04
Arm 05
Arm 07 x 4
Arm 06 x 4
Smol motor 2
cover new

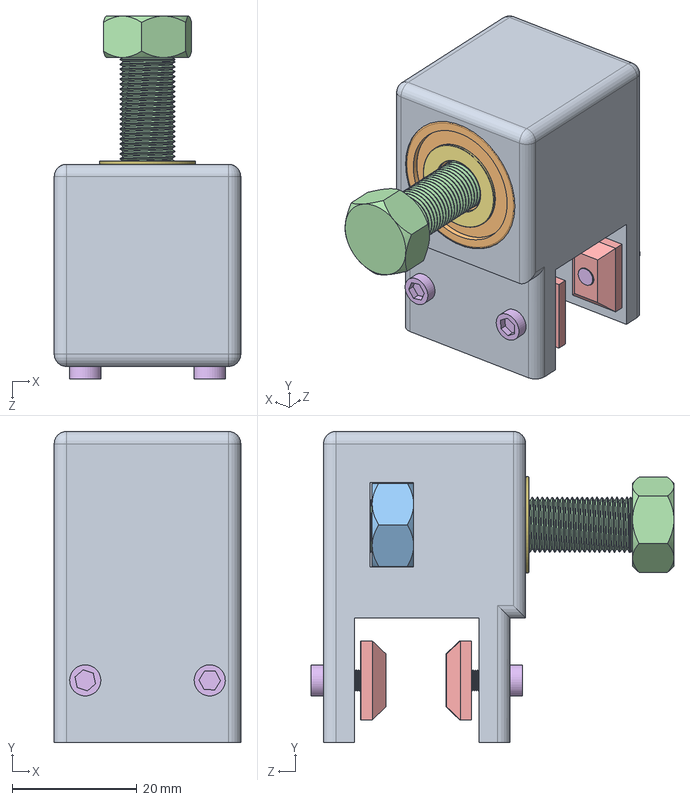
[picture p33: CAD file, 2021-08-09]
Mechanical design/Rocker Bogie/Differential/Connector to Diff.SLDASM
30.0 x 50.0 x 58.3 mm
Diiferential to body
double row cylindrical roller bearing_is
M8 Nut
M8 Bolt for differential
M3 T-nut x 4
M3 bolt x 4
Washer

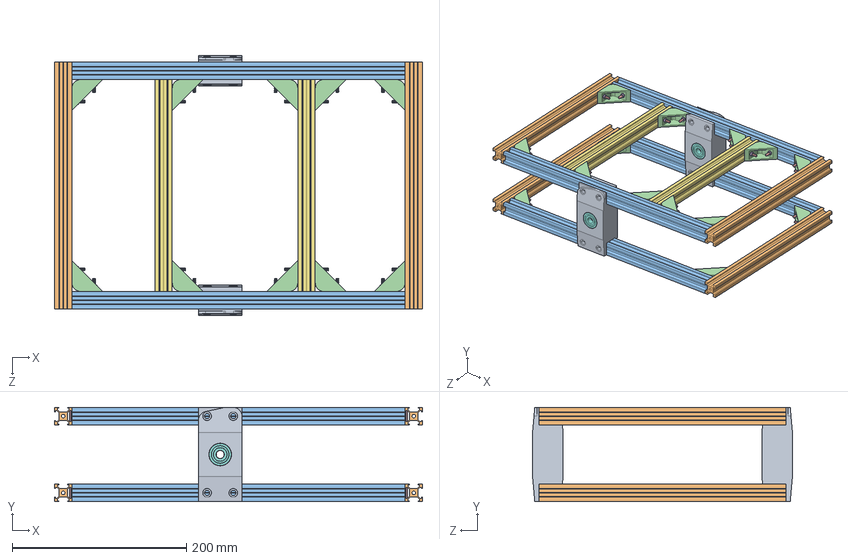
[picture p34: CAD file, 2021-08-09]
Mechanical design/Frame/Total Frame.SLDASM
422.0 x 108.0 x 298.0 mm
rocker to body x 2
T-slot aluminium profiles(283) x 4
T-slot aluminium profiles(382) x 4
connector x 14
T-bolt x 28
hexagon nut style 1_is x 28
T-slot aluminium profiles(243) x 2
double row radial ball bearing_is x 4

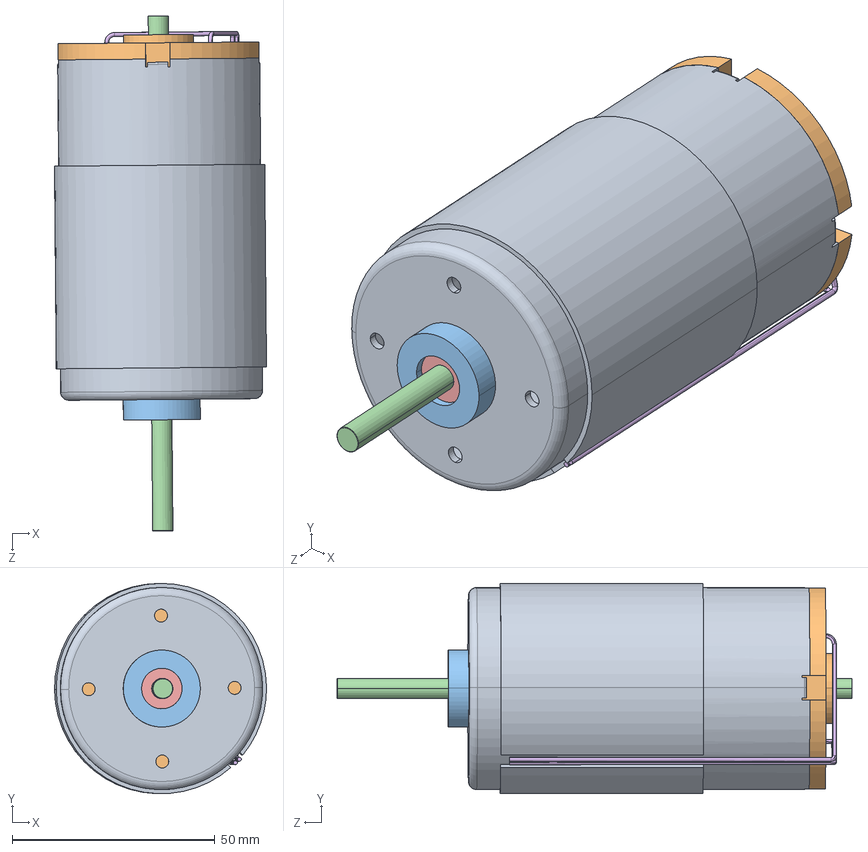
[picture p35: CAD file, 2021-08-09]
Mechanical design/Robotic arm/Large motor.SLDASM
52.3 x 51.9 x 127.0 mm
body Geometry.stp
Bott.stp
ARMICHER19V.stp
shaft.stp
Baring.stp
Wire.stp

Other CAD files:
Mechanical design/Antenna/Ultra High Frequency Antenna.SLDASM
Mechanical design/Rocker Bogie/Right side/Steering thor joint(RH).SLDASM
Mechanical design/Robotic arm/drill.SLDASM
Mechanical design/Rocker Bogie/Left side/Wheel + connector(left,back).SLDASM
Mechanical design/Antenna/High Gain Antenna (Part 1).SLDPRT
Mechanical design/Antenna/High Gain Antenna (Part 2).SLDPRT
Mechanical design/Antenna/High Gain Antenna (Part 3).SLDPRT
Mechanical design/Antenna/High Gain Antenna (Part 4).SLDPRT
Mechanical design/Antenna/Low Gain Antenna.SLDPRT
Mechanical design/Antenna/Ultra High Frequency Antenna(Part 1).SLDPRT
Mechanical design/Antenna/Ultra High Frequency Antenna(Part 2).SLDPRT
Mechanical design/Camera/Head.SLDPRT
Mechanical design/Camera/Lidar/Lidar.SLDPRT
Mechanical design/Camera/Lidar/Stand for lidar.SLDPRT
Mechanical design/Camera/Nuts and bolts for camera/M3 bolt for camera-1.SLDPRT
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

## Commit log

2021-08-05 Mechanical aspect - chassis
2021-08-06 Robotic arm added
2021-08-06 Added sw parts
    [Head.SLDPRT, Part1.SLDPRT, Part2.SLDPRT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]
2021-08-06 Added lidar parts
    [Lidar sensor.SLDASM, Lidar.SLDPRT, Stand for lidar.SLDPRT]
2021-08-06 Added nuts nad bolts for camera
    [M3 bolt for camera-1.SLDPRT, M3 bolt for camera-2.SLDPRT, M3 bolt for camera-3.SLDPRT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]
2021-08-06 added steppermotor parts
    [Stepper motor.SLDASM, shaft for stpmotor.SLDPRT, stepper motor-1.SLDPRT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]
2021-08-06 Added covers
    [Bottom cover.SLDPRT, Chassis side cover 1.SLDPRT, Chassis side cover 2 (Longer one).SLDPRT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]
2021-08-06 Added frame parts
    [Bottom Frame.SLDASM, Connector and Nut.SLDASM, T-slot aluminium profiles(243).SLDPRT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]
2021-08-06 added connectors sw
    [M3 T-nut.SLDPRT, M3 bolt.SLDPRT, M3 nut and bolt.SLDASM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]
2021-08-06 Added antenna parts
    [High Gain Antenna (Part 1).SLDPRT, High Gain Antenna (Part 2).SLDPRT, High Gain Antenna (Part 3).SLDPRT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]
2021-08-06 added arm sw
    [Arm 01.SLDPRT, Arm 02.SLDPRT, Arm 03.SLDPRT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]
2021-08-06 Added robotic arm parts
    [Base cylinder.SLDPRT, DRILL.SLDPRT, Drill connect.SLDPRT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]
2021-08-06 added differential parts
    [Connector to Diff.SLDASM, Differential.SLDPRT, Diiferential to body.SLDPRT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]
2021-08-06 added end joint bearing sw
    [Ball.SLDPRT, End join bearing.SLDASM, M5 bolt for end joint.SLDPRT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]
2021-08-06 Added left side rb sw
    [Bogie bolt.SLDPRT, Bogie nut.SLDPRT, Bolt servo connector.SLDPRT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]
2021-08-06 Added motor parts
    [Servo Assembly.SLDASM, Servo motor.SLDPRT, servo shaft.SLDPRT]
2021-08-06 Added right side parts
    [Bogie bolt(RH).SLDPRT, Bogie nut(RH).SLDPRT, Bolt servo connector(RH).SLDPRT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]
2021-08-06 c track.html
2021-08-06 Added track parts
    [1st track.SLDPRT, 2st track.SLDPRT]
2021-08-06 del track.html
2021-08-06 added wheel parts
    [Wheel Part-1.SLDPRT, Wheel Part-2.SLDPRT]
2021-08-06 Added final parts
    [Chassis 2.SLDPRT, Sampler Part1.SLDPRT, Wheel + motor for centre.SLDASM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]
